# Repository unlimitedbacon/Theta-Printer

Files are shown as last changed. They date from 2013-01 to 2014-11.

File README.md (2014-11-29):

Theta Printer
=============

The Theta Printer is a platform for printing with as many different materials as possible. Whether it be different colors of plastic, wood, carbon fiber, chocolate, or anything else you can make an extruder for. Each extruder moves simultaneously and independently, allowing the printer to lay down 4 different materials onto the same object at the same time. [See it in action.](https://www.youtube.com/watch?v=p_tqMAzWGm0)

A magnificent rendering of the Theta Printer
[Full Size](http://i.imgur.com/XjrklZc.jpg)

With most 3D printers, adding more extruders makes the machine slower and reduces the build volume. The Theta Printer overcomes this by using polar coordinates. A polar printer works kind of like an old fashioned record player. Your objects are printed onto a platter which spins. The advantage is that you can have many print heads. Each extruder is on the end of an arm which swings in and out. The spinning platter is called the ϴ ("theta") axis and the swinging arm is called the R axis. Together these replace the normal X and Y coordinates you're used to. A polar printer has a couple of advantages over normal cartesian 3D printers.

1. Less moving mass means better acceleration
2. Finer resolution, especially near the center
3. Multiple toolheads without reducing build area

The spinning platform makes this machine ideal for integrating a 3D scanner. In addition, you can easily swap out an extruder for a mill or any other tool, making the Theta Printer the perfect all-in-one fabrication machine.

Specs
-----
+ 4 extruders for multiple colors and materials
+ 320 mm build platter
+ 80425 mm^2 print area (bigger than most repraps)
+ 0.084 degrees/step angular resolution (ϴ Axis)
+ 0.20 mm/step linear resolution (R Axis)
+ Now comes in two versions! The lasercut edition and the reprap edition (printed parts & threaded rods)

Links
-----
* [Development progress](http://forums.reprap.org/read.php?185,178379)
* [Videos](https://www.youtube.com/channel/UC-gtCzj4NQnUl9iEiGGx9JA/videos)
* [Firmware](https://github.com/unlimitedbacon/Marlin)

ϴ Axis
------
A wooden disk, under which resides a complicated set of motors gears rods and bearings
[Full Size](http://i.imgur.com/GR4uxWu.png)

Objects are printed onto a platter that spins back and forth. Its driven via a stepper motor and a large gear. Rollers support the platter around the perimeter and keep it level.

R Axis
------
Four robotic arms arranged in a diamond shape
[Full Size](http://i.imgur.com/bllIclA.png)

Four Extruders are each mounted on the end of an arm that swings in and out. The blue protractor things are gears for moving the arms.

Z Axis
------
A set of four sprockets with the associated pulleys, motors, and drive belt
[Full Size](http://i.imgur.com/wnbYKVQ.png)

The Z axis is nothing new. Threaded rods in each corner are synchronized by a timing belt and driven by two stepper motors.

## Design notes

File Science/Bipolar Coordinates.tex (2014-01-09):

\documentclass[12pt,letterpaper]{report}
\usepackage[utf8]{inputenc}
\usepackage{amsmath}
\usepackage{amsfonts}
\usepackage{amssymb}
\usepackage{graphicx}
\author{Tyler Anderson}
\title{Bipolar Coordinates}
\begin{document}
\section*{Coordinate Conversion}

First off, things are complicated because this machine doesn't truly use polar coordinates. Normal polar coordinates consist of an angle and a distance ($\theta$ and r). But in our case, the extruder arms move in an arc and not a straight line. This means that our coordinates have to be represented by two angles. $\theta_1$ is the angle of rotation of the platter. $\theta_2$ is the angle of the arm. Since this system has two poles, we'll call it bipolar coordinates. 

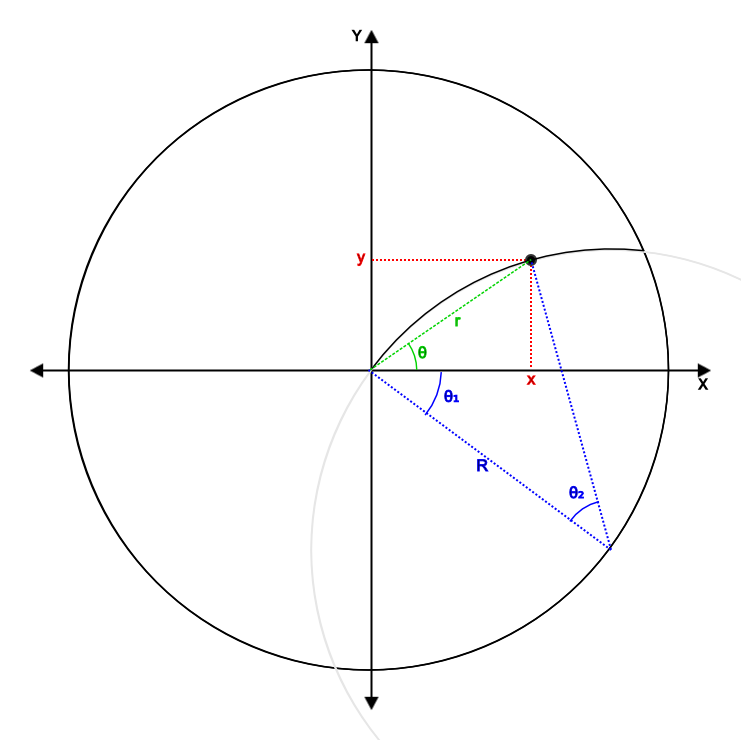
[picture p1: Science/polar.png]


In the above diagram, R is the length of the extruder arm which is 160mm on this machine. To simplify calculations all angles will be in radians.

The normal conversion from cartesian to polar is given by \ldots
\begin{equation}
	\theta = tan^{-1} \left( \dfrac{y}{x} \right)  
\end{equation}
\begin{equation}
	r = \sqrt{x^{2}+y^{2}}
\end{equation}

But for bipolar coordinates the conversion is \ldots
\begin{equation}
	\theta_2 = 2 sin^{-1} \left( \dfrac{\sqrt{x^2+y^2}}{2R} \right)
\end{equation}
\begin{equation}
	\theta_1 = \dfrac{\pi-\theta_2}{2} - tan^{-1} \left( \dfrac{y}{x} \right) 
\end{equation}

\section*{Parametric Equations}
We can now convert coordinates directly from cartesian to bipolar form, but more importantly, we need to know how to make the machine move in a straight line. Motion in 2D space is described using parametric equations. The equations for moving in a straight line in cartesian space are \ldots
\begin{equation}
	x = V_x t + x_0
\end{equation}
\begin{equation}
	y = V_y t + y_0
\end{equation}
\ldots where t is time, $V_x$ \& $V_y$ are the velocities in the $x$ and $y$ directions, and $x_0$ \& $y_0$ are the starting points.

By substituting these into the conversion for bipolar coordinates, we get the equations for linear motion in bipolar space.
\begin{equation}
	\theta_2 = 2 sin^{-1} \left(  \frac{\sqrt{(V_xt+x_0)^2 + (V_yt+y_0)^2}}{2R} \right)
\end{equation}
\begin{equation}
	\theta_1 = \frac{\pi-\theta_2}{2R} - tan^{-1} \left( \frac{V_y t + y_0}{V_x t + x_0} \right)
\end{equation}

\section*{Time}
The axes on the machine are controlled by stepper motors. Unlike most electric motors which run continuously when they are turned on, stepper motors move in small increments. In order to drive the motors, the controller needs to know exactly when to make each step. Since we know what the location of each axis will be after each step, we can solve for $t$ in the parametric equations to find out when to pulse the motors.

For $\theta_2$ the parametric equation is parabolic, so we must use the quadratic formula. The solution is broken down into components for simplicity.
\begin{equation}
	t_2 = \frac{-b\pm\sqrt{b^2-4ac}}{2a}
\end{equation}
\begin{equation}
	a = V_x^2+V_y^2
\end{equation}
\begin{equation}
	b = 2(V_x x_0 + V_y y_0)
\end{equation}
\begin{equation}
	c = x_o^2 + y_0^2 - 4R^2sin^2 \left( \frac{\theta_2}{2} \right)
\end{equation}

Remember that in the above equations, $\theta_2$ is the point after the next step will be made. It is easily determined by
\begin{equation}
	\theta_{2,n+1} = \theta_{2,n} \pm \Delta\theta_2
\end{equation}
where $\Delta\theta_2$ is the distance that axis moves with each step. $\Delta\theta_2$ is governed by the gear ratio and the number of steps per revolution of the motor.

The reason for the $\pm$ above is because we do not know in which direction the axis is moving (forward or backward) or if it will reverse direction before the step occurs. This means there are two possibilities. Combined with the two possible outcomes of the quadratic, this means that we can get up to 4 values for $t_2$. So which one do we choose? We use the lowest value that is still in the future ($> t$).

Now lets solve for $t$ in $theta_1$
\begin{equation}
	t_1 = \frac{x_0 * tan\left( \frac{\pi-\theta_2}{2} - \theta_1 \right) - y_0}{v_y - v_x * tan\left( \frac{\pi-\theta_2}{2} - \theta_1 \right)}
\end{equation}

But there is a problem. $\theta_1$ is dependent on $\theta_2$. In order to find $t$ we need to know $\theta_2$, but in order to get $\theta_2$ we need to know $t$. The solution we used is crude but effective. Instead of waiting until a certain time to make the step, the software periodically checks what the position of $\theta_1$ should be based on the current time. If the difference between the current and ideal positions is too great, it makes the step.

\section*{Derivatives}
It is also important for the software to know in which direction to move the motors, forward or reverse. When moving in a straight line in cartesian space, the direction is always the same. But in bipolar space, the direction can reverse in the middle of a move. In order to determine which way to go, we must find the signs of the derivatives of the parametric equations.

These are the derivatives. Here $x$ and $y$ are given by equations (5) and (6).
\begin{equation}
	\dfrac{d\theta_2}{dt} = \dfrac{2V_xx+2V_yy}{2R\sqrt{x^2+y^2}\sqrt{1-\dfrac{x^2+y^2}{4R^2}}}
\end{equation}
\begin{equation}
	\dfrac{d\theta_1}{dt} = -\left( \dfrac{1}{1-\dfrac{x^2+y^2}{4R^2}} \right) \left( \dfrac{(V_x^2+V_y^2)t+x_0V_x+y_0V_y}{2R\sqrt{x^2+y^2}} \right) - \left( \dfrac{1}{1+\left(\dfrac{y}{x}\right)^2} \right) \left( \dfrac{V_yx_0-V_xy_0}{x^2} \right) 
\end{equation}
\end{document}]{article}

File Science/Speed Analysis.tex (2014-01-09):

\documentclass[12pt,letterpaper]{report}
\usepackage[utf8]{inputenc}
\usepackage{amsmath}
\usepackage{amsfonts}
\usepackage{amssymb}
\usepackage{graphicx}
\usepackage{hyperref}
\author{Tyler Anderson}
\title{Theta Printer Speed Analysis}
\begin{document}

\maketitle

\section*{Speed Analysis}
The greatest limiting factor on the speeds of a 3D printer is the acceleration.

Older firmwares did not implement acceleration, so any changes in velocity would have to happen within the span of a single step. This limited the maximum speed of most printers to about 50 mm/s. While the motors and drive might be capable of much greater sustained speeds, the motor would not have enough torque to overcome the inertia of the moving parts, causing it to skip steps. Today's firmwares implement acceleration over multiple steps. By gradually ramping up the velocity, much higher maximum speeds can be achieved.

Today, the fastest reliable printer is probably the Ultimaker.

\subsection*{Motor Torque}
The RepRap forums recommend using stepper motors with a holding torque between 0.137 and 0.4 Newton-Meters \cite{rtorque}. Typical values for a NEMA 17 seem to be between 0.4 and 0.5 Nm \cite{htorque}. Our chosen motors are the NEMA 17s sold by Lulzbot with an advertised holding torque of 0.55 Nm.

Unfortunately, the torque exerted by a motor varies with speed. Also, torque while in motion is always significantly less than the holding torque. The datasheet for our chosen motors \cite{lulzmotor} provides a graph of the torque curve. At high speed the torque ranges from 0.25 to 0.20 Nm. We will accept 0.225 Nm as the average value.
\begin{equation}
	\tau = 0.225~\mathrm{Nm}
\end{equation}

% Probably uneccesary since torque at the platter can be found directly from the gear ratio
\subsection*{Motor Force}
In order to find the force exerted by the motor, we must first determine the radius of the motor gear. We use 18~tooth gears with a 2~mm pitch.
\begin{equation}
	r = \dfrac{18~\mathrm{teeth}*2.00~\dfrac{\mathrm{mm}}{\mathrm{tooth}}}{2\pi} = 5.73~\mathrm{mm} = 0.00573~\mathrm{m}
\end{equation}
\begin{equation}
	F = \dfrac{\tau}{r} = \dfrac{0.225~\mathrm{Nm}}{0.00573~\mathrm{m}} = 39.3~\mathrm{N}
\end{equation}

\subsection*{Mass Moment of Inertia}
Solidworks provides these figures based on the CAD model. $I_p$ will be the mass moment of inertia of the platter and associated moving parts.
% Needs to be redone since we changed to the aluminium platter
\begin{equation}
	I_p = ~\mathrm{kg*mm^2}
\end{equation}

It is slightly more difficult to get the figure for an extruder arm because the CAD model does not include the extruder itself. We must estimate the MMI of an extruder around the appropriate axis and add it to the figure given by Solidworks.

Approximating the extruder as a point mass:
\begin{equation}
	I_e = mr^2 = 
\end{equation}

Adding to the figure given for the arm by Solidworks, we get the total mass moment of inertia for the extruder arm.
\begin{equation}
	I_a = 0.00370601782~\mathrm{kg*m^2} +
\end{equation}

\subsection*{Final Torque}
The torque exerted on the platter and arms can be directly calculated from the motor torque and gear ratios.

For the platter:
\begin{equation}
	\tau_p = \tau \dfrac{N_2}{N_1} = 0.225~\mathrm{Nm} * \dfrac{385~\mathrm{teeth}}{18~\mathrm{teeth}} = 4.81~\mathrm{Nm}
\end{equation}

For the arm:
\begin{equation}
	\tau_a = \tau \dfrac{N_2}{N_1} = 0.225~\mathrm{Nm} * \dfrac{450~\mathrm{teeth}}{18~\mathrm{teeth}} = 5.63~\mathrm{Nm}
\end{equation}

\subsection*{Acceleration}
The angular acceleration can be found by the angular adaption of Newton's second law.
\begin{equation}
	\tau = I\alpha
\end{equation}

For the platter:
\begin{equation}
	\alpha_p = \dfrac{\tau_p}{I_p} = \dfrac{4.81~\mathrm{Nm}}{•} = ~\mathrm{\dfrac{rad}{s^2}}
\end{equation}

For the arm:
\begin{equation}
	\alpha_a = \dfrac{\tau_a}{I_a} = \dfrac{5.63~\mathrm{Nm}}{•} = ~\mathrm{\dfrac{rad}{s^2}}
\end{equation}

Since the extruder is fixed on the end of the arm, and the radius is constant, we can calculate the linear acceleration of the $\theta_2$ axis.
\begin{equation}
	a = \alpha r
\end{equation}
\begin{equation}
	a_a = ~\mathrm{\dfrac{rad}{s^2}} * 160~\mathrm{mm} = ~\mathrm{\dfrac{mm}{s^2}}
\end{equation}

For comparison, we can also calculate the linear acceleration of the $theta_1$ axis at a certain radius. The printer is designed to match the resolution of a RepRap at $r=122.55~\mathrm{mm}$.
\begin{equation}
	a_p = ~\mathrm{\dfrac{rad}{s^2}} * 122.55~\mathrm{mm} = ~\mathrm{\dfrac{mm}{s^2}}
\end{equation}
Closer to the center the acceleration will be less, but farther from the center it will be greater.

\subsection*{Equivalent Mass}
For comparison with other printers, we can also calculate the equivalent mass of each axis. These are the masses that a Cartesian printer would have to have to achieve the same acceleration.

\begin{equation}
	m = \dfrac{F}{a}
\end{equation}
X axis:
\begin{equation}
	m_x = \dfrac{39.3~\mathrm{N}}{~\mathrm{\dfrac{mm}{s^2}}} = ~\mathrm{g}
\end{equation}
Y axis:
\begin{equation}
	m_y = \dfrac{39.3~\mathrm{N}}{~\mathrm{\dfrac{mm}{s^2}}} = ~\mathrm{g}
\end{equation}

\section*{Comparison with Current RepRaps}
\subsection*{Mass of Moving Components}
\begin{tabular}{c|c|c}
& X Axis (g) & Y Axis (g) \\ 
\hline 
Modified Sells Mendel & 700 & 1300 \\ 
\hline 
Printxel & 400 & 800 \\ 
\end{tabular}

\subsection*{Acceleration}
\begin{tabular}{c|c}
Firmware & Acceleration ($mm/s^2$) \\
\hline
Marlin Defaults \cite{marlin} & 3000 \\
\hline
Safe Values for RepRap & 1500 \\
\hline
Ultimaker & 4600 \\
\hline
Accelerated Ultimaker \cite{ultimax} & 8000 \\
\hline
Cupcake w/o Acceleration & 38400 \\
\end{tabular}

\begin{thebibliography}{99}
\bibitem{rtorque} \url{http://reprap.org/wiki/Stepper_motor#Holding_Torque}
\bibitem{htorque} \url{http://reprap.org/wiki/Stepper_motor#NEMA_17_suppliers}
\bibitem{lulzmotor} \url{http://download.lulzbot.com/AO-100/hardware/electronics/spec_sheets/SY42STH47-1504A_stepperMotors.pdf}
\bibitem{marlin} \url{https://github.com/ErikZalm/Marlin/blob/Marlin_v1/Marlin/Configuration.h}
\bibitem{ultimax} \url{http://www.youtube.com/watch?v=i3DGRFMsU00}
\end{thebibliography}

\end{document}

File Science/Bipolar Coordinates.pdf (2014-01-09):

## Coordinate Conversion

First off, things are complicated because this machine doesn’t truly use polar coordinates. Normal polar coordinates consist of an angle and a distance (θ and r). But in our case, the extruder arms move in an arc and not a straight line. This means that our coordinates have to be represented by two angles. θ1 is the angle of rotation of the platter. θ2 is the angle of the arm. Since this system has two poles, we’ll call it bipolar coordinates.

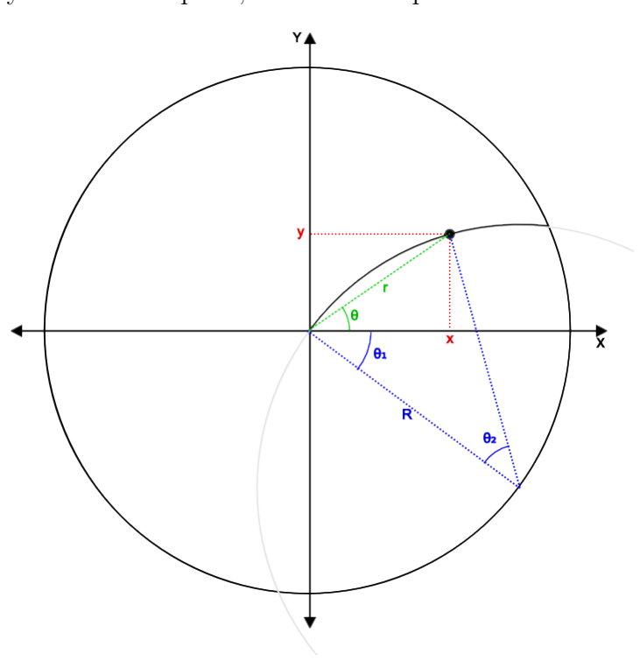
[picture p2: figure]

In the above diagram, R is the length of the extruder arm which is 160mm on this machine. To simplify calculations all angles will be in radians.
The normal conversion from cartesian to polar is given by . . .

θ = tan⁻¹

y
x
(1)

r =

p
x

2 + y

2
(2)

1

But for bipolar coordinates the conversion is . . .

θ2 = 2sin⁻¹

p
x

2 + y

2
2R

!
(3)

θ1 =

π − θ2
2

− tan⁻¹

y
x
(4)

## Parametric Equations

We can now convert coordinates directly from cartesian to bipolar form, but more importantly, we need to know how to make the machine move in a straight line. Motion in 2D space is described using parametric equations. The equations for moving in a straight line in cartesian space are . . .

x = Vxt + x0 | (5)
y = Vyt + y0 | (6)

. . . where t is time, Vx & Vy are the velocities in the x and y directions, and x0 & y0 are the starting points.
By substituting these into the conversion for bipolar coordinates, we get the equations for linear motion in bipolar space.

θ2 = 2sin⁻¹

p
(Vxt + x0)

2 + (Vyt + y0)

2
2R

!
(7)

θ1 =

π − θ2
2R

− tan⁻¹

Vyt + y0
Vxt + x0
(8)

## Time

The axes on the machine are controlled by stepper motors. Unlike most elec-tric motors which run continuously when they are turned on, stepper motors move in small increments. In order to drive the motors, the controller needs to know exactly when to make each step. Since we know what the location of each axis will be after each step, we can solve for t in the parametric equations to find out when to pulse the motors.

2

For θ2 the parametric equation is parabolic, so we must use the quadratic formula. The solution is broken down into components for simplicity.

t2 =

−b ±

√
b

2 − 4ac
2a

(9)

a = V

2
x + V

2
y

(10)

b = 2(Vxx0 + Vyy0) | (11)

c = x

2
o + y

2
0 − 4R

2

sin²

θ2
2
(12)

Remember that in the above equations, θ2 is the point after the next step will be made. It is easily determined by

θ2,n+1 = θ2,n ± ∆θ2 | (13)

where ∆θ2 is the distance that axis moves with each step. ∆θ2 is governed by the gear ratio and the number of steps per revolution of the motor.
The reason for the ± above is because we do not know in which direction the axis is moving (forward or backward) or if it will reverse direction before the step occurs. This means there are two possibilities. Combined with the two possible outcomes of the quadratic, this means that we can get up to 4 values for t2. So which one do we choose? We use the lowest value that is still in the future (> t).
Now lets solve for t in theta1

t1 =

x0 ∗ tan

π−θ2
2 − θ1
− y0
vy − vx ∗ tan

π−θ2
2 | − θ1
| (14)

But there is a problem. θ1 is dependent on θ2. In order to find t we need to know θ2, but in order to get θ2 we need to know t. The solution we used is crude but effective. Instead of waiting until a certain time to make the step, the software periodically checks what the position of θ1 should be based on the current time. If the difference between the current and ideal positions is too great, it makes the step.

3

## Derivatives

It is also important for the software to know in which direction to move the motors, forward or reverse. When moving in a straight line in cartesian space, the direction is always the same. But in bipolar space, the direction can reverse in the middle of a move. In order to determine which way to go, we must find the signs of the derivatives of the parametric equations. These are the derivatives. Here x and y are given by equations (5) and (6).
dθ2
dt =

2Vxx + 2Vyy

2R

p
x

2 + y

2

r
1 −

x

2 + y

2
4R²

(15)

dθ1
dt = −

1

1 −

x

2 + y

2
4R²

(V

2
x + V

2
y

)t + x0Vx + y0Vy

2R

p
x

2 + y

2

!
−

1
1 + y
x

2

Vyx0 − Vxy0
x

2

(16)

4

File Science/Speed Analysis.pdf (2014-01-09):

# Theta Printer Speed Analysis

### Tyler Anderson

### November 29, 2013

## Speed Analysis

The greatest limiting factor on the speeds of a 3D printer is the acceleration. Older firmwares did not implement acceleration, so any changes in velocity would have to happen within the span of a single step. This limited the maximum speed of most printers to about 50 mm/s. While the motors and drive might be capable of much greater sustained speeds, the motor would not have enough torque to overcome the inertia of the moving parts, caus-ing it to skip steps. Today’s firmwares implement acceleration over multiple steps. By gradually ramping up the velocity, much higher maximum speeds can be achieved.
Today, the fastest reliable printer is probably the Ultimaker.

### Motor Torque

The RepRap forums recommend using stepper motors with a holding torque between 0.137 and 0.4 Newton-Meters [1]. Typical values for a NEMA 17 seem to be between 0.4 and 0.5 Nm [2]. Our chosen motors are the NEMA 17s sold by Lulzbot with an advertised holding torque of 0.55 Nm. Unfortunately, the torque exerted by a motor varies with speed. Also, torque while in motion is always significantly less than the holding torque. The datasheet for our chosen motors [3] provides a graph of the torque curve. At high speed the torque ranges from 0.25 to 0.20 Nm. We will accept 0.225 Nm as the average value.
τ = 0.225 Nm | (1)

### Motor Force

In order to find the force exerted by the motor, we must first determine the radius of the motor gear. We use 18 tooth gears with a 2 mm pitch.

r =

18 teeth ∗ 2.00

mm
tooth
2π
= 5.73 mm = 0.00573 m | (2)

F =

τ
r

=

0.225 Nm
0.00573 m
= 39.3 N | (3)

1

### Mass Moment of Inertia

Solidworks provides these figures based on the CAD model. Ip will be the mass moment of inertia of the platter and associated moving parts.

Ip = kg ∗ mm²
(4)

It is slightly more difficult to get the figure for an extruder arm because the CAD model does not include the extruder itself. We must estimate the MMI of an extruder around the appropriate axis and add it to the figure given by Solidworks.
Approximating the extruder as a point mass:
Ie = mr² = | (5)

Adding to the figure given for the arm by Solidworks, we get the total mass moment of inertia for the extruder arm.

Ia = 0.00370601782 kg ∗ m

2+ | (6)

### Final Torque

The torque exerted on the platter and arms can be directly calculated from the motor torque and gear ratios.
For the platter:

τp = τ

N2
N1

= 0.225 Nm ∗

385 teeth
18 teeth = 4.81 Nm | (7)

For the arm:

τa = τ

N2
N1

= 0.225 Nm ∗

450 teeth
18 teeth = 5.63 Nm | (8)

### Acceleration

The angular acceleration can be found by the angular adaption of Newton’s second law.
τ = Iα | (9)

For the platter:

αp =

τp
Ip

=

4.81 Nm
ffl

=

rad
s

2

(10)

2

For the arm:
αa =

τa
Ia

=

5.63 Nm
ffl

=

rad
s

2

(11)

Since the extruder is fixed on the end of the arm, and the radius is constant, we can calculate the linear acceleration of the θ2 axis.

a = αr | (12)

aa =

rad
s

2

∗ 160 mm =

mm
s

2

(13)

For comparison, we can also calculate the linear acceleration of the theta1 axis at a certain radius. The printer is designed to match the resolution of a RepRap at r = 122.55 mm.

ap =

rad
s

2

∗ 122.55 mm =

mm
s

2

(14)

Closer to the center the acceleration will be less, but farther from the center it will be greater.

### Equivalent Mass

For comparison with other printers, we can also calculate the equivalent mass of each axis. These are the masses that a Cartesian printer would have to have to achieve the same acceleration.

m =

F
a

(15)

X axis:
mx =

39.3 N
mm
s

2

= g | (16)

Y axis:
my =

39.3 N
mm
s

2

= g | (17)

3

## Comparison with Current RepRaps

### Mass of Moving Components

| X Axis (g) | Y Axis (g)
Modified Sells Mendel | 700 | 1300
Printxel | 400 | 800

### Acceleration

Firmware | Acceleration (mm/s²
)
Marlin Defaults [4] | | 3000
Safe Values for RepRap | | 1500
Ultimaker | | 4600
Accelerated Ultimaker [5] | | 8000
Cupcake w/o Acceleration | | 38400

4

# Bibliography

[1] http://reprap.org/wiki/Stepper_motor#Holding_Torque
[2] http://reprap.org/wiki/Stepper_motor#NEMA_17_suppliers
[3] http://download.lulzbot.com/AO-100/hardware/electronics/spec_sheets/SY42STH47-1504A_stepperMotors.pdf (http://download.lulzbot.com/AO-100/hardware/electronics/spec_sheets/SY42STH47-1504A_stepperMotors.pdf)
[4] https://github.com/ErikZalm/Marlin/blob/Marlin_v1/Marlin/Configuration.h (https://github.com/ErikZalm/Marlin/blob/Marlin_v1/Marlin/Configuration.h)
[5] http://www.youtube.com/watch?v=i3DGRFMsU00

5

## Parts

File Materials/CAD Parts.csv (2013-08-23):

ITEM NO. | PART NUMBER | DESCRIPTION | QTY.
1 | Head Holder |  | 8
2 | Arm Rod |  | 8
3 | M8.Nut |  | 149
4 | Arm Center |  | 4
5 | Arm Axis Rod |  | 4
6 | R Gear |  | 4
7 | M3x16.Bolt.91290A120 |  | 172
8 | Extruder Mount Plate |  | 4
9 | M4x30.Bolt.91280A148 |  | 8
10 | M4.Nut.90591A141 |  | 8
11 | Level 1 Corner |  | 8
12 | 608RS Bearing |  | 36
13 | 608 Bearing Cap |  | 1
14 | M3.Nut.90591A121 |  | 172
15 | R Motor Mount |  | 4
16 | Base |  | 7
17 | Cuerpo |  | 7
18 | Tapa |  | 7
19 | B18.6.7M - M3 x 0.5 x 5 Type I Cross Recessed PHMS --5N |  | 28
20 | Eje |  | 7
21 | AFBMA 12.1.4.1 - 0050-11 - 10 SI NC 10_68 |  | 14
22 | M3x10.Bolt.91290A115 |  | 28
23 | Motor.Sprocket |  | 7
24 | Theta Center |  | 1
25 | M3x30.Bolt.91290A130 |  | 4
26 | Level Z Corner |  | 4
27 | Linear Bearing Body |  | 8
28 | Linear Bearing inside |  | 8
29 | Platter Rod |  | 4
30 | Theta Motor Mount |  | 1
31 | Platter Top |  | 1
32 | Platter Bottom |  | 1
33 | M3x16.Countersunk.Bolt.91294A134 |  | 4
34 | Platter Axle |  | 1
35 | M8.Washer.91455A130 |  | 8
36 | Theta Gear |  | 1
37 | Platter Roller Mount High |  | 1
38 | M8x20.Bolt.91310A533 |  | 3
39 | Platter Roller Mount Low |  | 2
40 | Level 4 Corner |  | 4
41 | Z Smooth Rod |  | 8
42 | Z Rod |  | 4
43 | Z.Rod.Sprocket.a_6z51-036df0610 |  | 4
44 | Smooth Rod Clamp |  | 16
45 | Belt1-1 |  | 1
46 | Level 1 Side |  | 1
47 | Level 2 Side |  | 1
48 | Level 4 Side |  | 1
49 | M8x30.Bolt.91310A536 |  | 4
50 | Side 1 |  | 2
51 | Side 2 |  | 2
52 | 91166A210 |  | 8

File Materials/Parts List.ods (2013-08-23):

Acquired? | Printed Parts | Description | Qty
✓ | Head Holder |  | 8
✓ | Level 1 Corner |  | 8
✓ | Motor Sprocket |  | 7
✓ | Arm Center |  | 4
✓ | Level 4 Corner |  | 4
✓ | Level Z Corner |  | 4
✓ | R Motor Mount |  | 4
✓ | Z Rod Sprocket |  | 4
✓ | Platter Roller Middle |  | 3
✓ | Theta Center |  | 1
✓ | Theta Motor Mount |  | 1
 | Laser Cut Parts | Description | Qty | Cost
3 | R Gear | 5mm Acrylic | 4
✓ | Theta Gear | 5mm Acrylic | 1
✓ | Extruder Mount Plate | 5mm Plywood | 4
✓ | Platter Top | 5mm Plywood | 1
✓ | Platter Bottom | 5mm Plywood | 1
✓ | Level 1 Side | 5mm Plywood | 1
✓ | Level 2 Side | 5mm Plywood | 1
✓ | Level 4 Side | 5mm Plywood | 1
✓ | Side 1 | 5mm Plywood | 2
✓ | Side 2 | 5mm Plywood | 2
✓ | 608 Bearing Cap | 5mm Plywood | 1
✓ | Platter Roller Side High |  | 4
✓ | Platter Roller Side Low |  | 2
 | Total |  |  | $60
 | Threaded Rods | Description | Qty | Length (mm) | Total Length | Purchase Qty | Price/Meter | Subtotal
✓ | Arm Rod | M8 1.25 Pitch | 8 | 220 | 1760 | 2000
✓ | Arm Axis Rod | M8 1.25 Pitch | 4 | 110 | 440 | 1000
✓ | Platter Rod | M8 1.25 Pitch | 4 | 400 | 1600 | 2000
✓ | Platter Axle | M8 1.25 Pitch | 1 | 55 | 55 | 1000
✓ | Z Rod | M8 1.25 Pitch | 4 | 430 | 1720 | 2000
✓ | Total |  |  |  | 5575 | 8000 | 4.29 | $34.32 | McMaster | 99055A125 | http://www.mcmaster.com/#catalog/119/3147/=liic32
 | Smooth Rod
✓ | Z Smooth Rod | M8 | 8 | 350 | 2800 | 3200 |  | $49.56 | AliExpress | 707204369 | http://www.aliexpress.com/item/CNC-2pcs-Linear-shaft-400mm-long-diameter-8mm-L-400mm-harden-linear-rod-round-shaft-chrome/707204369.html
 |  |  |  |  |  | 12ft |  | $27.28 | McMaster | 89095K15 | http://www.mcmaster.com/#89095K15
 | Vitamins | Description | Qty | Purchase Qty | Price Each | Subtotal | Supplier | Part # | Link
✓ | 608ZZ Bearing |  | 28 | 50 |  | 22.5 | AliExpress | 609983490 | http://www.aliexpress.com/item/50pcs-lot-608ZZ-608-2RS-8-22-7-Deep-groove-ball-bearing-skate-wheel-bearing/609983490.html
✓ | LM8UU Linear Bearing |  | 8 | 20 |  | 13.8 | AliExpress | 488396282 | http://www.aliexpress.com/item/LM8UU-8mm-Linear-Ball-Bearing-Bush-Bushing-New/488396282.html
✓ | M3.Nut.90591A121 |  | 172 | 200 |  | 2.78 | McMaster | 90591A121 | http://www.mcmaster.com/#catalog/119/3167/=l4j9dm
✓ | M3x10.Bolt.91290A115 |  | 28 | 100 |  | 5.02 | McMaster | 91290A115 | http://www.mcmaster.com/#catalog/119/3093/=l4j9n6
✓ | M3x16.Bolt.91290A120 |  | 176 | 200 |  | 12.1 | McMaster | 91290A120 | http://www.mcmaster.com/#catalog/119/3093/=l4j9rl
✓ | M3x16.Countersunk.Bolt.91294A134 |  | 4 | 100 |  | 11.67 | McMaster | 91294A134 | http://www.mcmaster.com/#catalog/119/3102/=l4ja5r
✓ | M3x30.Bolt.91290A130 |  | 4 | 0 |  | 0 | McMaster | 91290A130 | http://www.mcmaster.com/#catalog/119/3093/=l4jb78
✓ | M4.Nut.90591A141 |  | 8 | 100 |  | 1.39 | McMaster | 90591A141 | http://www.mcmaster.com/#catalog/119/3167/=l4jbpz
✓ | M4x30.Bolt.91280A148 |  | 8 | 100 |  | 7.96 | McMaster | 91280A148 | http://www.mcmaster.com/#catalog/119/3129/=l4jcc0
✓ | M8.Nut | 1.25mm Pitch | 149 | 200 |  | 9.02 | McMaster | 90592A022 | http://www.mcmaster.com/#hex-nuts/=l4je22
✓ | M8.Washer.91455A130 |  | 8 | 100 |  | 6.09 | McMaster | 91455A130 | http://www.mcmaster.com/#catalog/119/3202/=l4jej3
✓ | M8x20.Bolt.91310A533 |  | 3 | 0 |  | 0 | McMaster | 91310A533 | http://www.mcmaster.com/#catalog/119/3128/=l4jf1j
✓ | M8x30.Bolt.91310A536 |  | 4 | 25 |  | 7.91 | McMaster | 91310A536 | http://www.mcmaster.com/#standard-cap-screws/=ld4026
 | Motor.Sprocket | 18 Grooves | 7 | 0 | 5.81 | 0 | SDP/SI | A 6T16M018DF6005 | https://sdp-si.com/eStore/PartDetail.asp?Opener=Group&PartID=42977&GroupID=347
✓ | Z Belt | GT2 1210.00 mm | 1 | 1 | 9.32 | 9.32 | SDP/SI | A 6R51M605060 | https://sdp-si.com/eStore/PartDetail.asp?Opener=Order&PartID=75945&GroupID=342&Qty=0
✓ | Z Belt | GT2 1228.00 mm | 1 | 1 | 9.32 | 9.32 | SDP/SI | A 6R51M614060 | https://sdp-si.com/eStore/PartDetail.asp?Opener=Order&PartID=75946&GroupID=342&Qty=0
 | Z.Rod.Sprocket | 36 Grooves | 4 | 0 | 6.18 | 0 | SDP/SI | A 6Z51-036DF0610 | https://sdp-si.com/eStore/PartDetail.asp?Opener=Group&PartID=55833&GroupID=218
 | Total |  |  |  |  | $118.88
 | Electronics | Description | Qty | Cost
✓ | ATX Power Supply |  | 1 | $100
 | Decapede Electronics |  | 1 | 250
 | Stepper Drivers | Polulu compatible | 10 | 99.5
6 | NEMA 17 Motors |  | 7 | 97.65
 |  |  |  | $547
 | Extruder Components |  | Qty | Price Each | Subtotal | Link
 | Printed Parts
✓ | Greg's Wade Reloaded Extruder |  | 4 |  |  | http://www.thingiverse.com/thing:18379
 | Hot End
✓ | Lulzbot Budaschnozzle |  | 4 | 95 | 380 | http://www.lulzbot.com/?q=products/budaschnozzle-20-w-035mm-nozzle
 | Extruder Motor
✓ | NEMA 17 |  | 4 | 13.95 | 55.8 | http://www.lulzbot.com/?q=products/nema-17-stepper-motors
 | Extruder Hardware
✓ | M8 Hobbed Bolt |  | 4 | 7 | 28 | http://www.lulzbot.com/?q=products/hobbed-bolt-stainless-steel
✓ | M8 Washer |  | 16
✓ | M3x8 Bolt |  | 12
✓ | M3x30 Bolt |  | 4
✓ | M3 Nut |  | 4
✓ | M3 Washer |  | 16
✓ | M4x55 Bolt |  | 8
✓ | M4x20 Bolt | Duplicate? | 8
✓ | M4 Nut | Duplicate? | 16
✓ | 608ZZ Bearing |  | 12
✓ | M8x20 Rod |  | 4
✓ | Spring | .297OD, .049WD, .669FL? | 8
 |  |  |  |  | 463.8
 | Grand Total | $1,274

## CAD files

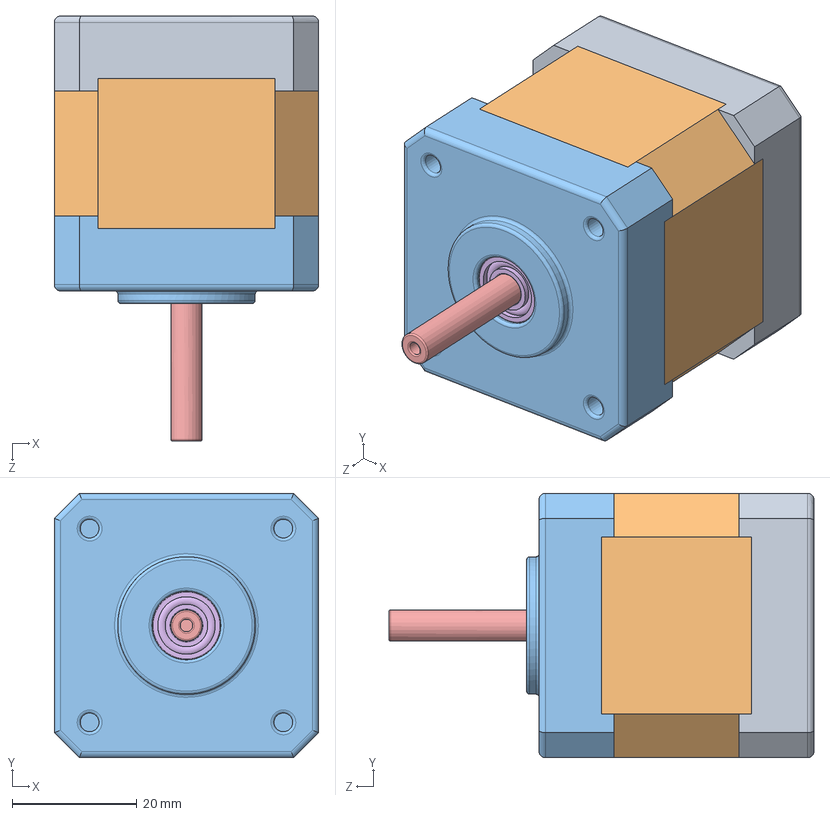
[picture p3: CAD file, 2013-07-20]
Vitamins/NEMA 17/NEMA 17.SLDASM
42.3 x 42.3 x 68.0 mm
Base
Cuerpo
Tapa
pan cross head_am
Eje
instrument ball bearing_68_am

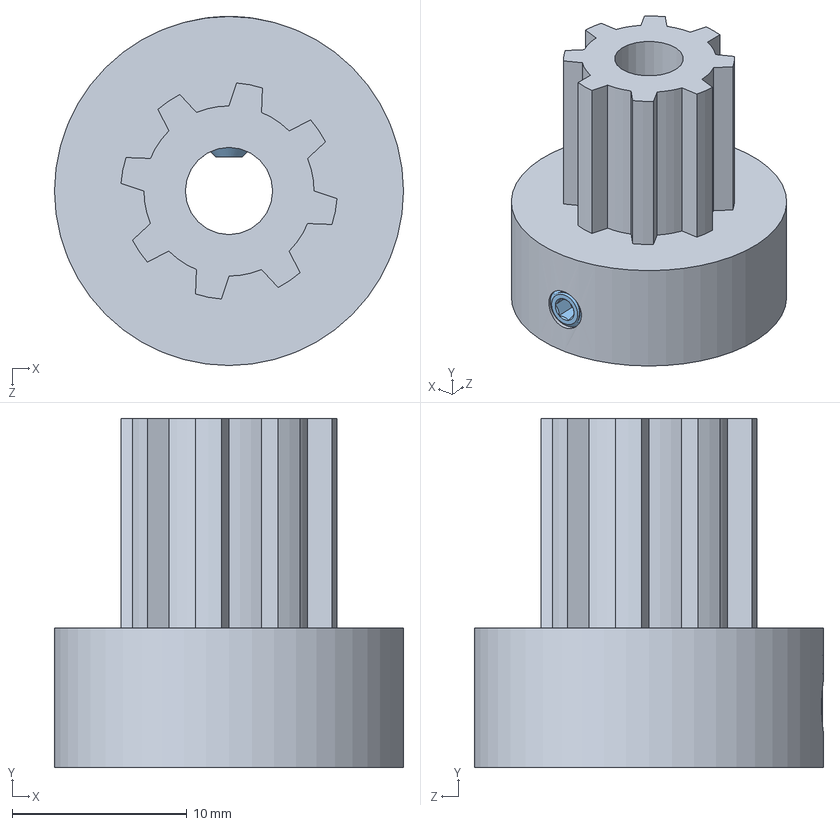
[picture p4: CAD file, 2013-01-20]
Vitamins/FULLER_LOCK_PULLEY/FULLER LOCK PULLEY.SLDASM
20.0 x 20.0 x 20.0 mm
FULLER LOCK PULLEY
3mm Nylon Nut
3mm X 8 SET SCREW ( Mcmaster 92015A105)

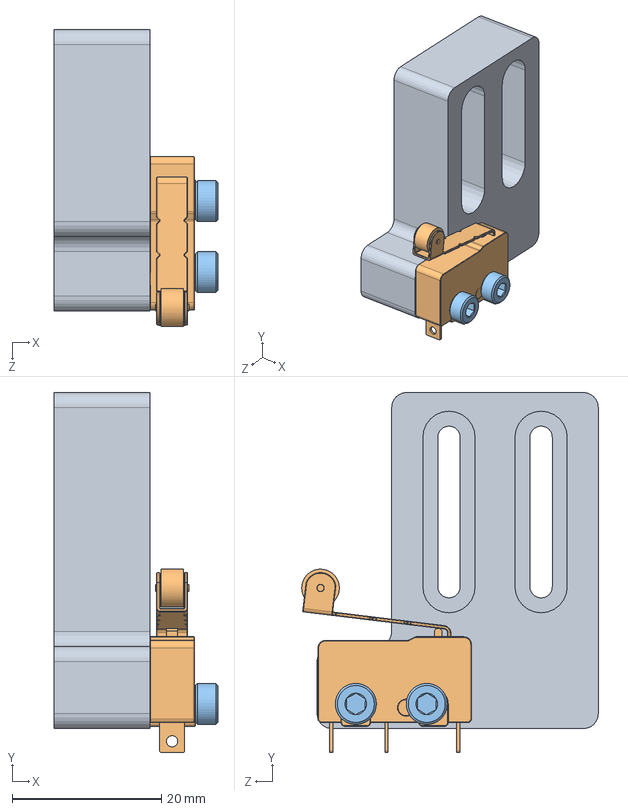
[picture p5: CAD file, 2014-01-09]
Endstop Mount Assembly.SLDASM
21.9 x 48.2 x 39.7 mm
Endstop Mount
SM5.Microswitch
M3x16.Bolt.91290A120 x 2

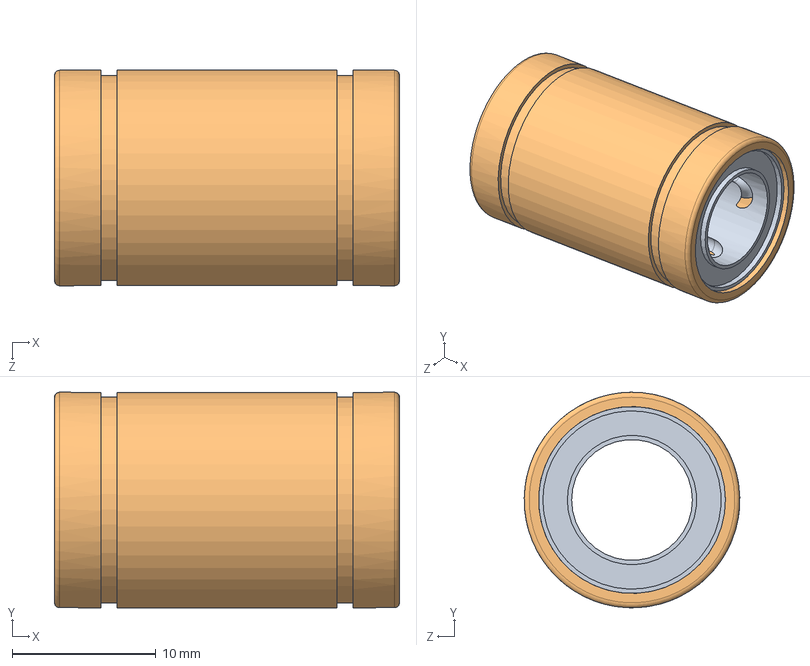
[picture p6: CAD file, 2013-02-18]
Vitamins/LM8UU/Linear Bearing animation.SLDASM
24.0 x 15.0 x 15.0 mm
Linear Bearing Body
Linear Bearing inside

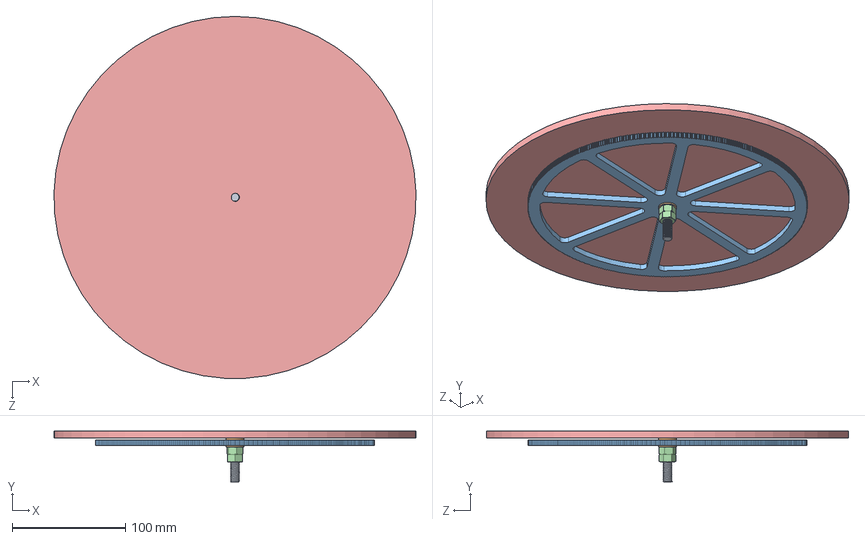
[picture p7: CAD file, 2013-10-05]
Platter Assembly.SLDASM
319.9 x 45.0 x 320.0 mm
Platter Axle
M8.Washer.91455A130 x 2
Theta Gear
M8.Nut x 2
Platter

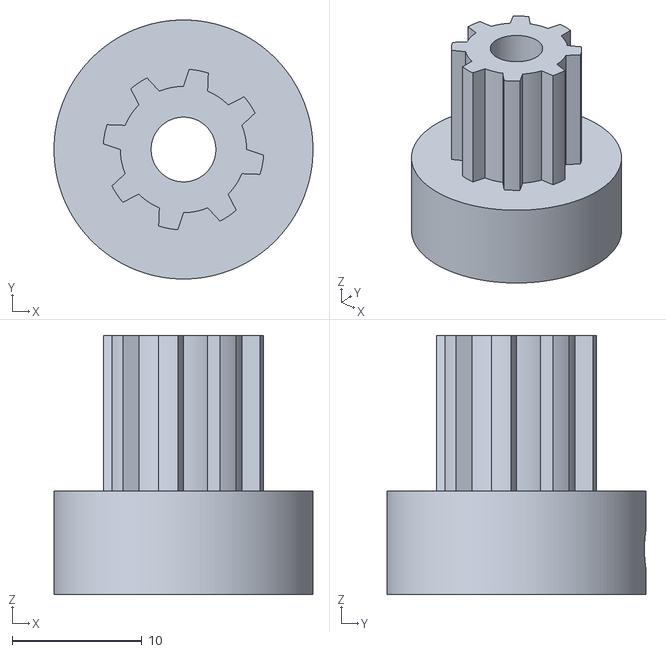
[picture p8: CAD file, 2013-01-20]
Vitamins/FULLER_LOCK_PULLEY/FULLER_LOCK_PULLEY_OVERSIZED.STL
20.0 x 20.0 x 20.0

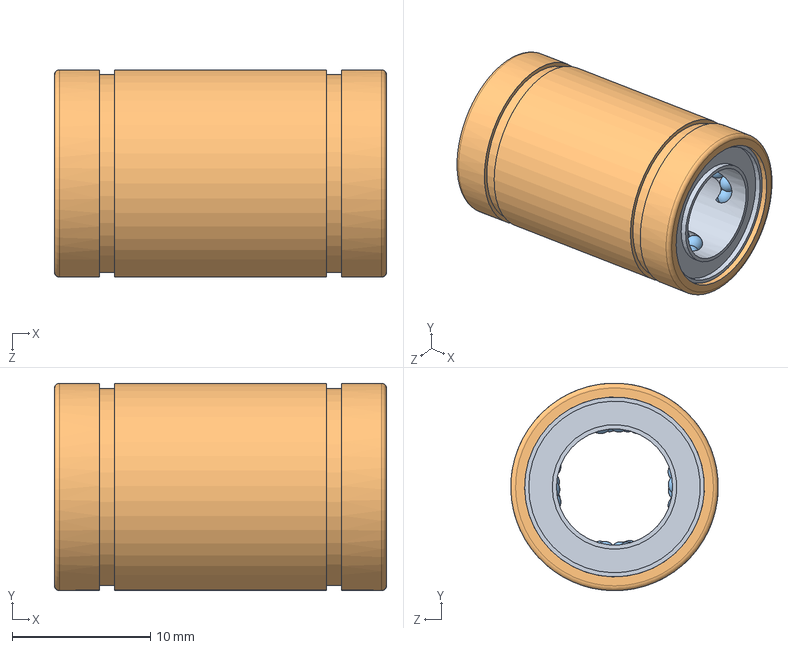
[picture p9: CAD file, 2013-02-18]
Vitamins/LM8UU/LU8MM.SLDASM
24.0 x 15.0 x 15.0 mm
Linear Bearing Body
Linear Bearing inside
Municion x 102

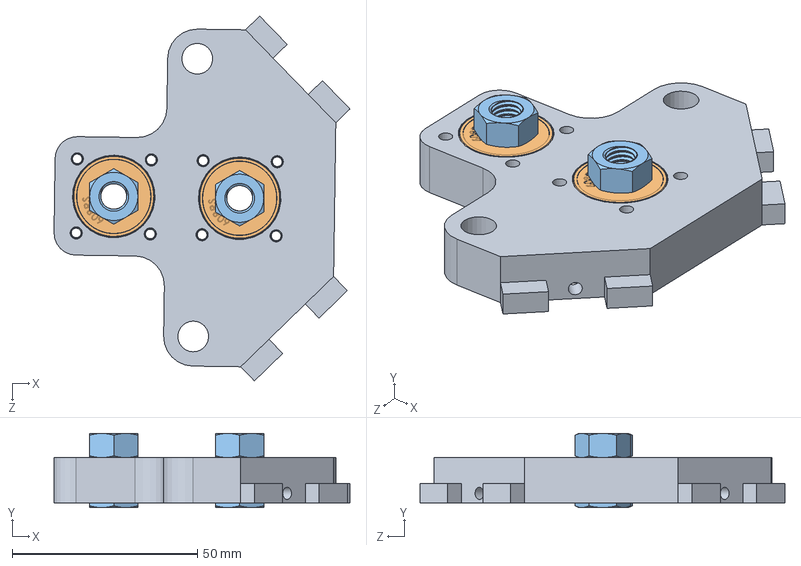
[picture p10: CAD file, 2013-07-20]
Level 1 Corner Assembly.SLDASM
79.9 x 20.0 x 98.5 mm
Level 1 Corner
608RS Bearing x 2
M8.Nut x 4
M3.Nut.90591A121 x 8

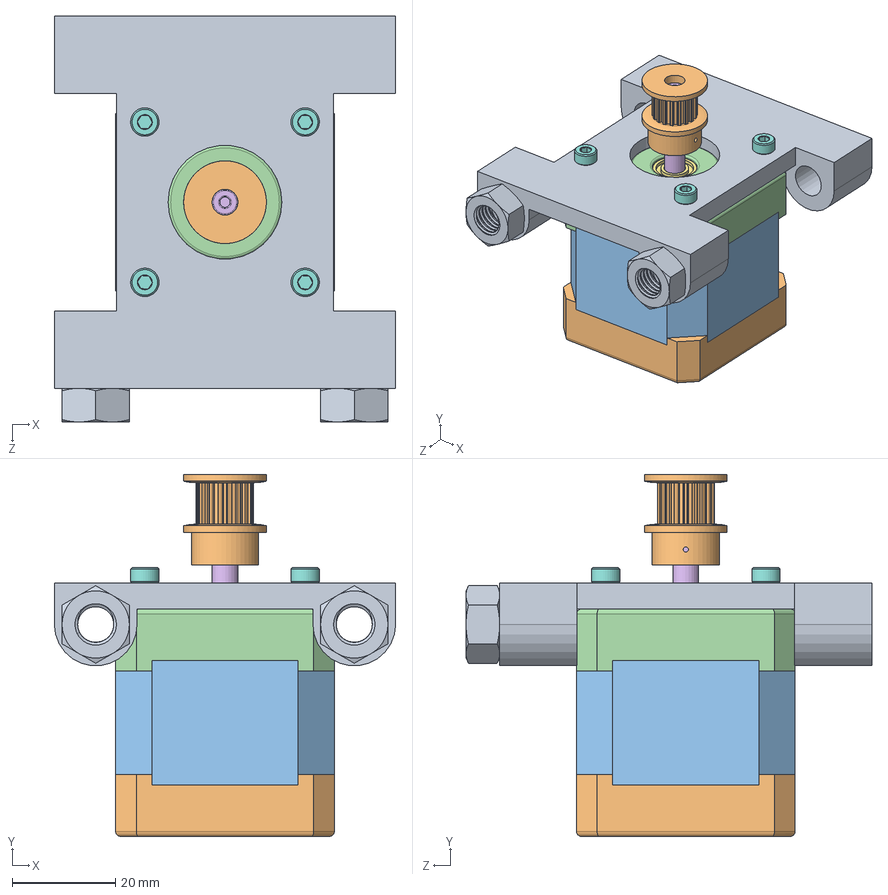
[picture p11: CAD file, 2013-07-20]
Theta Motor Assembly.SLDASM
66.0 x 70.0 x 78.5 mm
Theta Motor Mount
Base
Cuerpo
Tapa
pan cross head_am
Eje
instrument ball bearing_68_am
M3x10.Bolt.91290A115 x 4
M8.Nut x 2
Motor.Sprocket

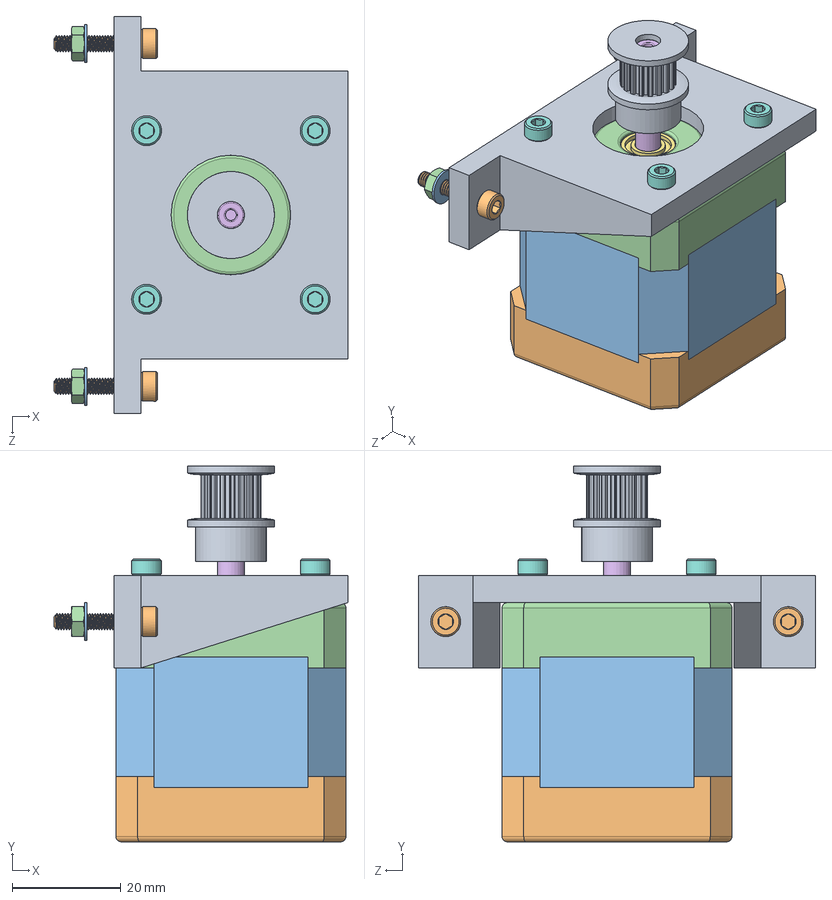
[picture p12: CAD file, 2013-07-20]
R Motor Assembly.SLDASM
54.0 x 69.1 x 73.0 mm
R Motor Mount
Base
Cuerpo
Tapa
pan cross head_am
Eje
instrument ball bearing_68_am
M3x10.Bolt.91290A115 x 4
Motor.Sprocket
M3x16.Bolt.91290A120 x 2
M3.Washer.91166A210 x 2
M3.Nut.90591A121 x 2

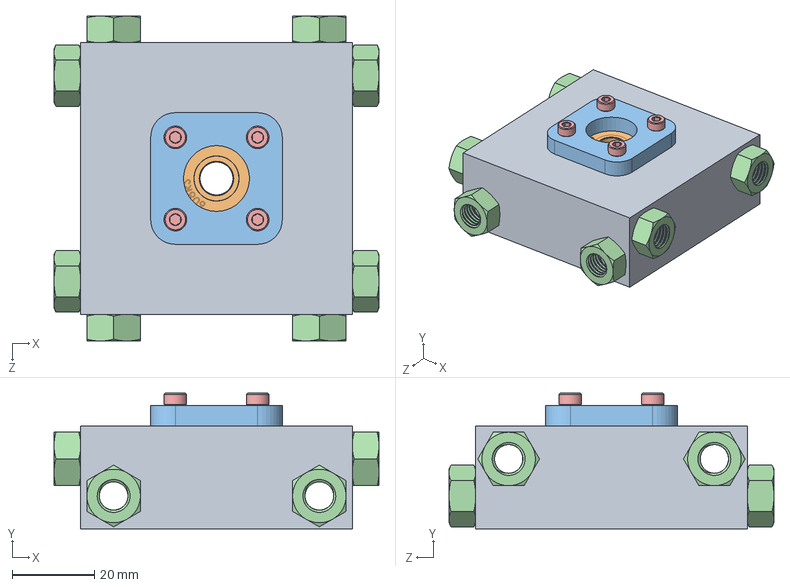
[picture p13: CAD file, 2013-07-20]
Theta Center Assembly.SLDASM
79.0 x 33.0 x 79.0 mm
Theta Center
608RS Bearing
608 Bearing Cap
M8.Nut x 8
M3x16.Bolt.91290A120 x 4
M3.Nut.90591A121 x 4

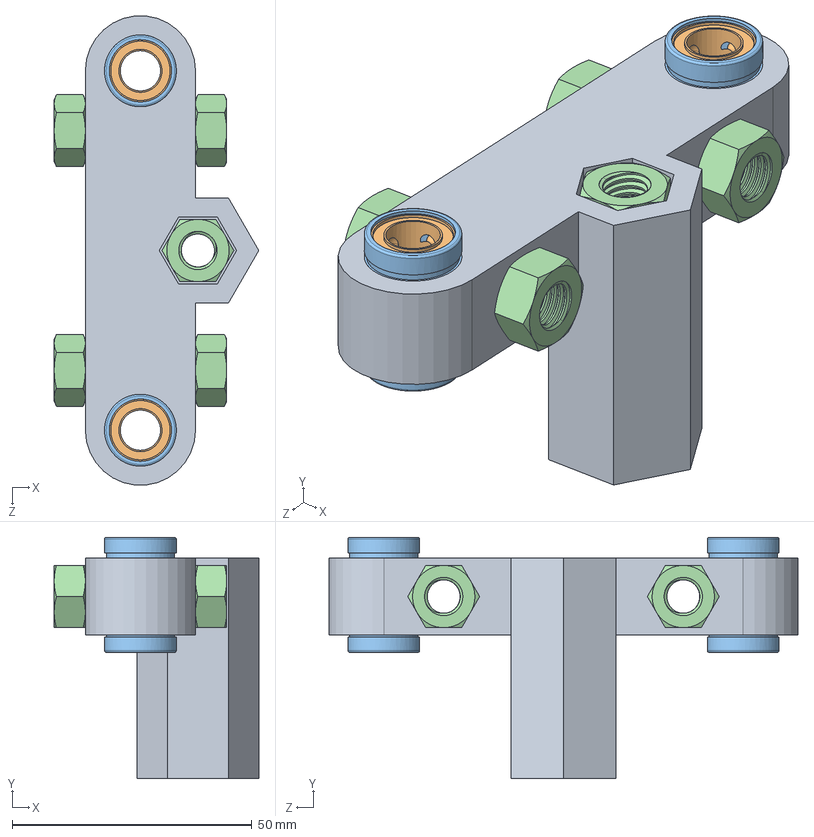
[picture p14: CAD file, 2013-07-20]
Level Z Corner Assembly.SLDASM
42.7 x 50.3 x 97.9 mm
Level Z Corner
Linear Bearing Body x 2
Linear Bearing inside x 2
M8.Nut x 5

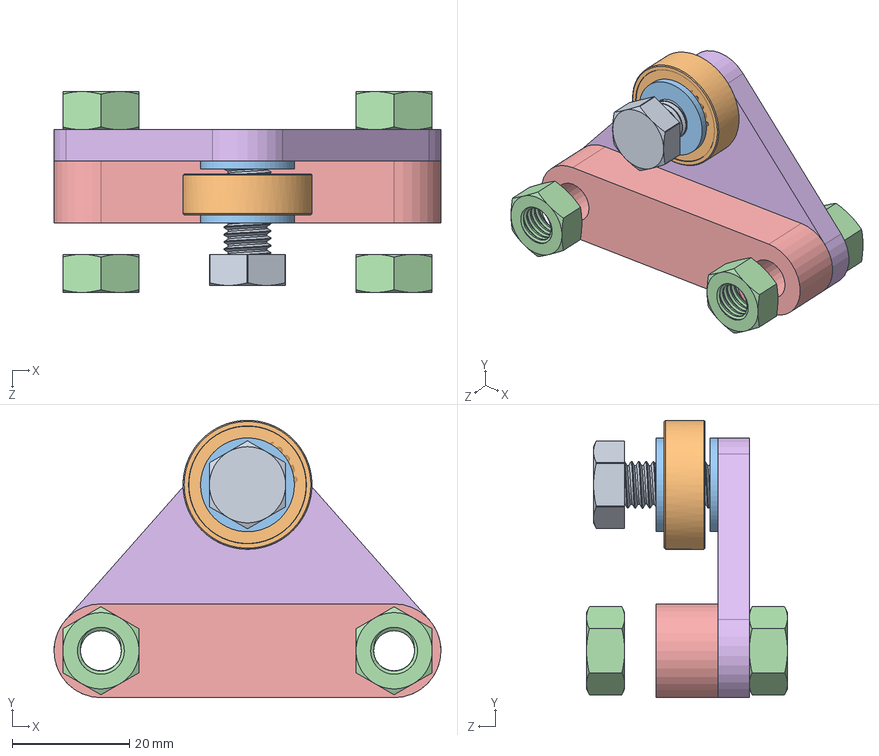
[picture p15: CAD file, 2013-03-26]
Platter Roller Assembly.SLDASM
66.0 x 47.3 x 34.3 mm
M8x20.Bolt.91310A533
608RS Bearing
M8.Washer.91455A130 x 2
M8.Nut x 4
Platter Roller Middle
Platter Roller Side

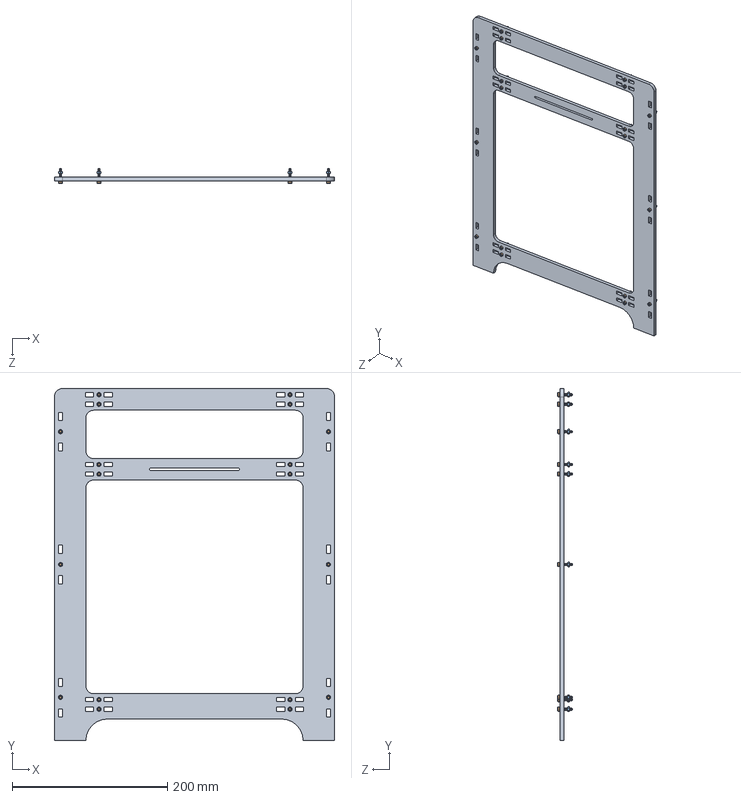
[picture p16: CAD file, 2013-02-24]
Side 2 Assembly.SLDASM
361.3 x 453.7 x 19.0 mm
Side 2
M3x16.Bolt.91290A120 x 18
M3.Nut.90591A121 x 18

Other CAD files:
Vitamins/LM8UU/LM8UU.SLDASM
Side 1 Assembly.SLDASM
Smooth Rod Clamp Assembly.SLDASM
Platter Roller Assembly High.SLDASM
608 Bearing Cap.SLDPRT
Arm Center.SLDPRT
Belt1-1.sldprt
Bottom Sketch.SLDPRT
DXFs/608 Bearing Cap.DXF
DXFs/Extruder Mount Plate.DXF
DXFs/Level 1 Side.DXF
DXFs/Level 2 Side.DXF
DXFs/Level 4 Side.DXF
DXFs/Platter Bottom.DXF
DXFs/Platter Roller Side.High.DXF
DXFs/Platter Roller Side.Low.DXF
DXFs/Platter Top.DXF
DXFs/R Gear.DXF
DXFs/Side 1.DXF
DXFs/Side 2.DXF
DXFs/Theta Gear.DXF
Endstop Mount.SLDPRT
Endstop Mount.STP
Extruder Fan Mount.SLDPRT
Extruder Fan Mount.stp
Extruder Mount Plate.SLDPRT
Head Holder.SLDPRT
Level 1 Corner.SLDPRT
Level 1 Side.SLDPRT
Level 2 Side.SLDPRT
Level 4 Corner.SLDPRT
Level 4 Side.SLDPRT
Level Z Corner.SLDPRT
Materials/CAD Parts.SLDDRW
Platter Roller Assembly Low.SLDASM
Platter Roller Middle.SLDPRT
Platter Roller Mount High.SLDPRT
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

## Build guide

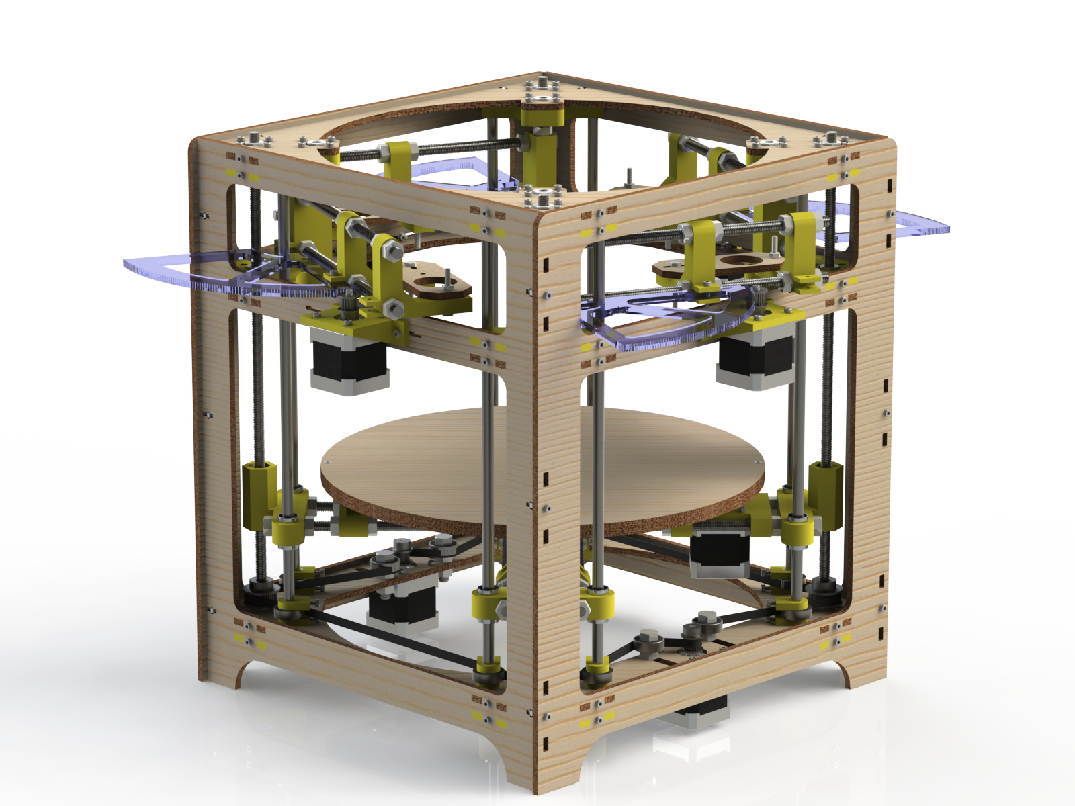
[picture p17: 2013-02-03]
Renders/theta_printer_12.png

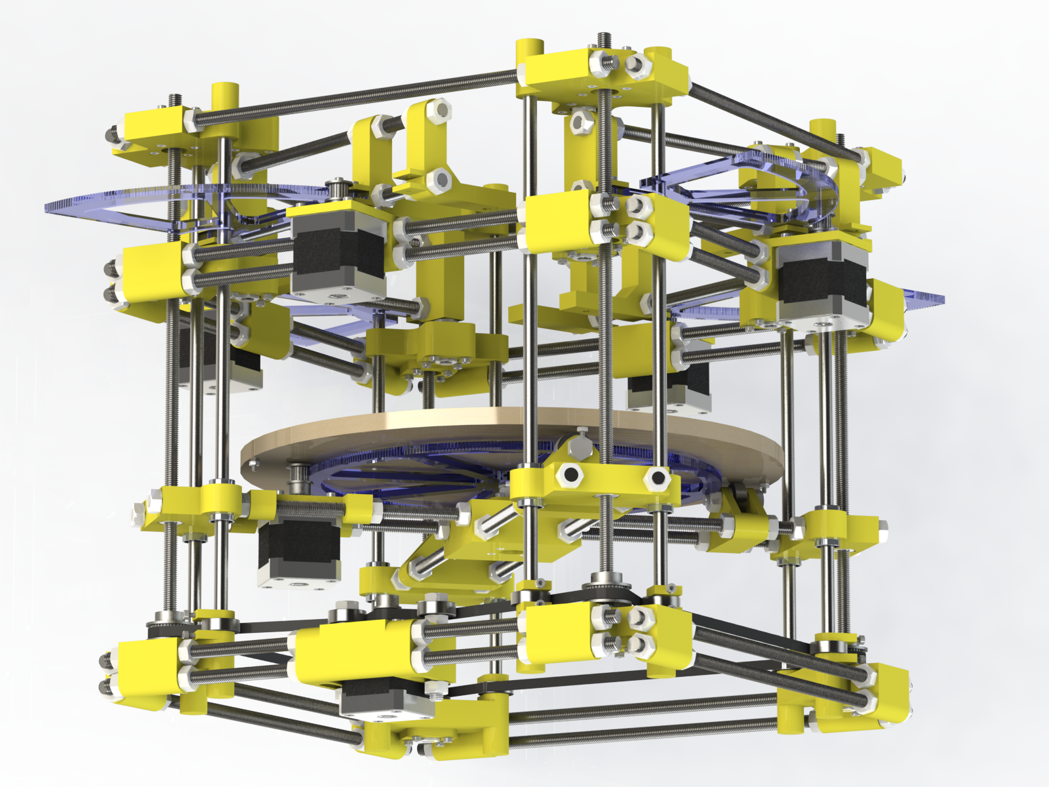
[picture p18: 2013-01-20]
Renders/theta_printer_10.png

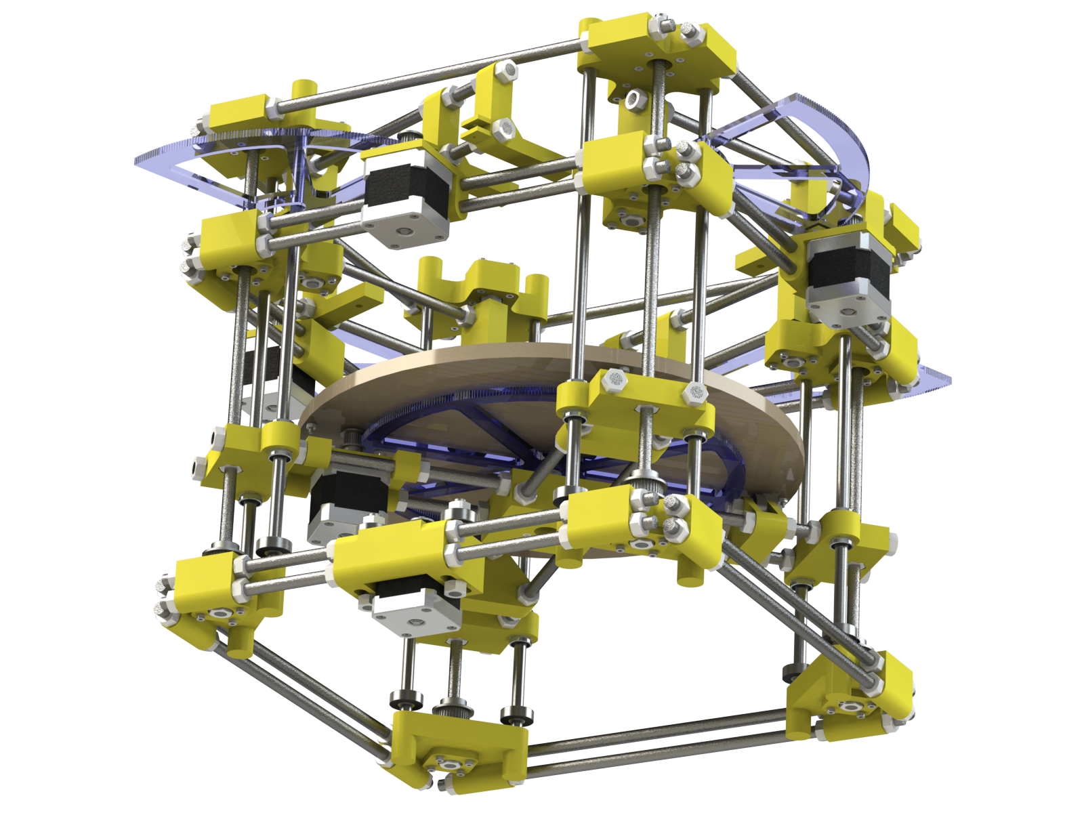
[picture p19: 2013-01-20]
Renders/theta_printer_8.png

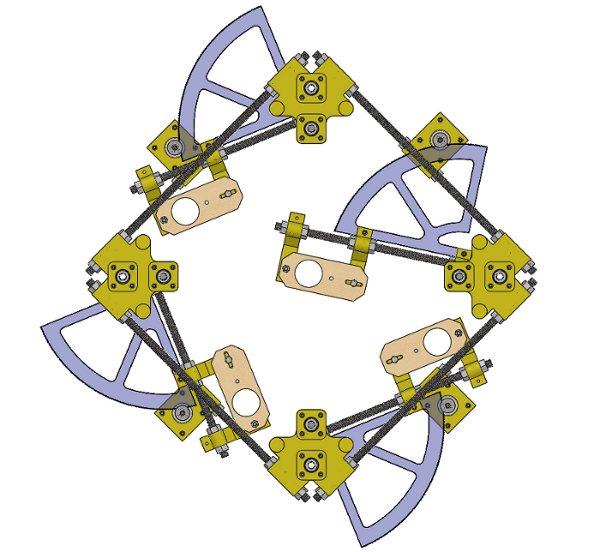
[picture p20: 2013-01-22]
Renders/Top Quad Assembly Extended.scaled.png

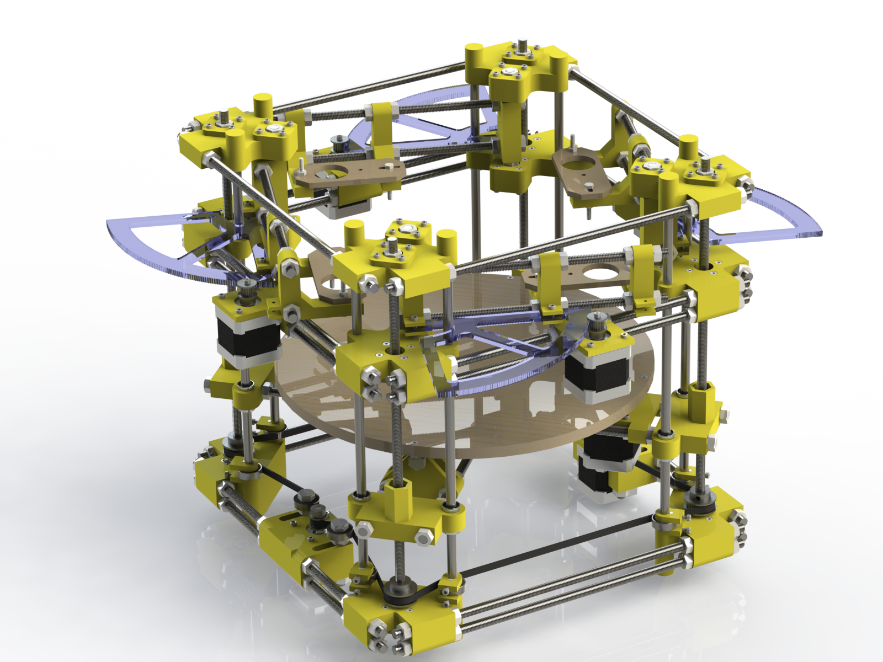
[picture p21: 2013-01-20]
Renders/theta_printer_11.png

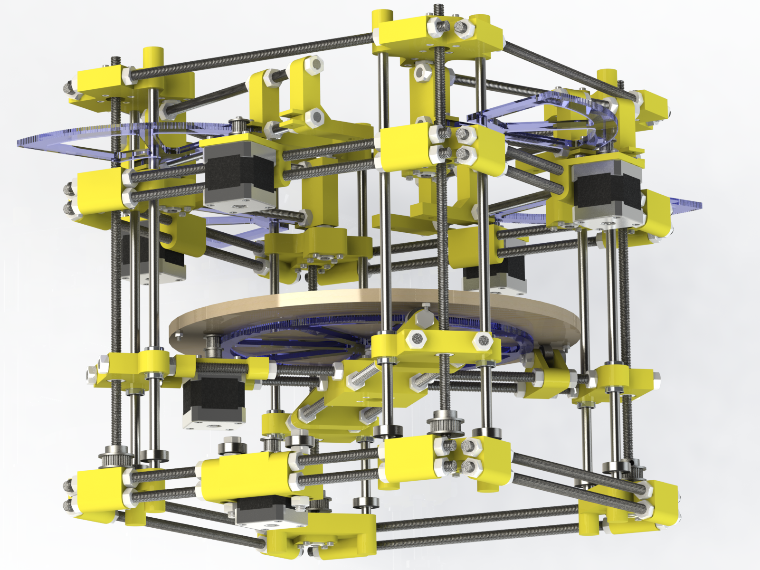
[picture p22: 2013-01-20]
Renders/theta_printer_9.png

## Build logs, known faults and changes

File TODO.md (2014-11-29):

* Square nuts
* Shallower captive nut holes on the big square
* Even gear ratio on theta (so theres an even number of steps per rotation)
* tolerances (rod holes, bearing holes, captive nuts, etc.)
* Thicken frame near Z tensioners and other thin spots
* Move tensioners farther from motors so washers don't cover motor mounting bolts
* theta gear with teeth on inside, bolted to platter around perimeter, with rollers under the gear
* way to adjust theta motor position
* Arange rollers in proper tripod
* slice top off theta drive gear
* method for adjusting phase between halves of theta gear, to eliminate play
	* Use 3 layers. Horizontal screw in middle layer to adjust phase.
* deeper teeth on theta gear
* Z smooth rods are slightly longer than 400mm. add room in level 4 corners
* platter does not fit out through sides
* M3x16 bolts are not long enough to reach through corners. recommend M3x20
* Procedure for aligning level Z with smooth rods: assemble frame with 2 sides only and level z in middle. push in smooth rods through bottom. adjust level z corner nuts until rods align with level 2 holes
* Hammer smooth rods into bottom corners first.
* You doofus. The extruders collide when one moves into the center. Even when the rest are fully retracted.
* Screwdriver notches on printed parts, to easily pry them off the print surface.
* Extend endstop mount slots to the left.
* Locks that slide onto hex nuts on the arm shafts. This will hold the arms in place when not in use and hold the nuts so you can torque things for assembly/callibration.
* The platter can unscrew itself from the shaft at inconvenient times (for example, during your senior design project presentation).
* Notches in frame to allow middle section rods to be unscrewed. Or better yet, some better means for detatching/removing the Z section. How about hinged clamp things on the corner pieces so you can detatch the middle section rods.
* Z probe
* Don't make extruders out of PLA
* Bowden extruders. Imagine 4 Krakens O_o
* Threaded rods should slide freely through printed parts
* Collision switches on extruders
* Extruder arm rods should be arranged horizontally instead of vertically.
* Bed heater needs 24V PSU and probably slip ring rated for higher power.
* Bed thermistor is probably totally wrong
* Opto sensor for homeing platter. This is not critical but could be useful for restarting paused prints.
* Connect platter gear to motor with belt.
* Need some way to clean nozzles when switching extruders
* **Ditch the whole bipolar thing and rebase everything on the R-360**
	* option for independent Z axis or locked Z axis
* Motor dampers

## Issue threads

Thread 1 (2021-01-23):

Straight R axis

n0p0n3, 2021-01-23:
I was wondering if the R axis has to be curved, or if it could be straight. Im think of a system of either linear actuators or a showerhead like matrix as a print head for a electrodisposition based system

n0p0n3, 2021-01-24:
Also, i’ve seen that you can merge the theta and z axis to have one motor with high pitch count thread do both, ie have one complete rotation of the theta axis raise the z axis by one mm or so. Do you have any thoughts on how well this would work, or problems with this method?

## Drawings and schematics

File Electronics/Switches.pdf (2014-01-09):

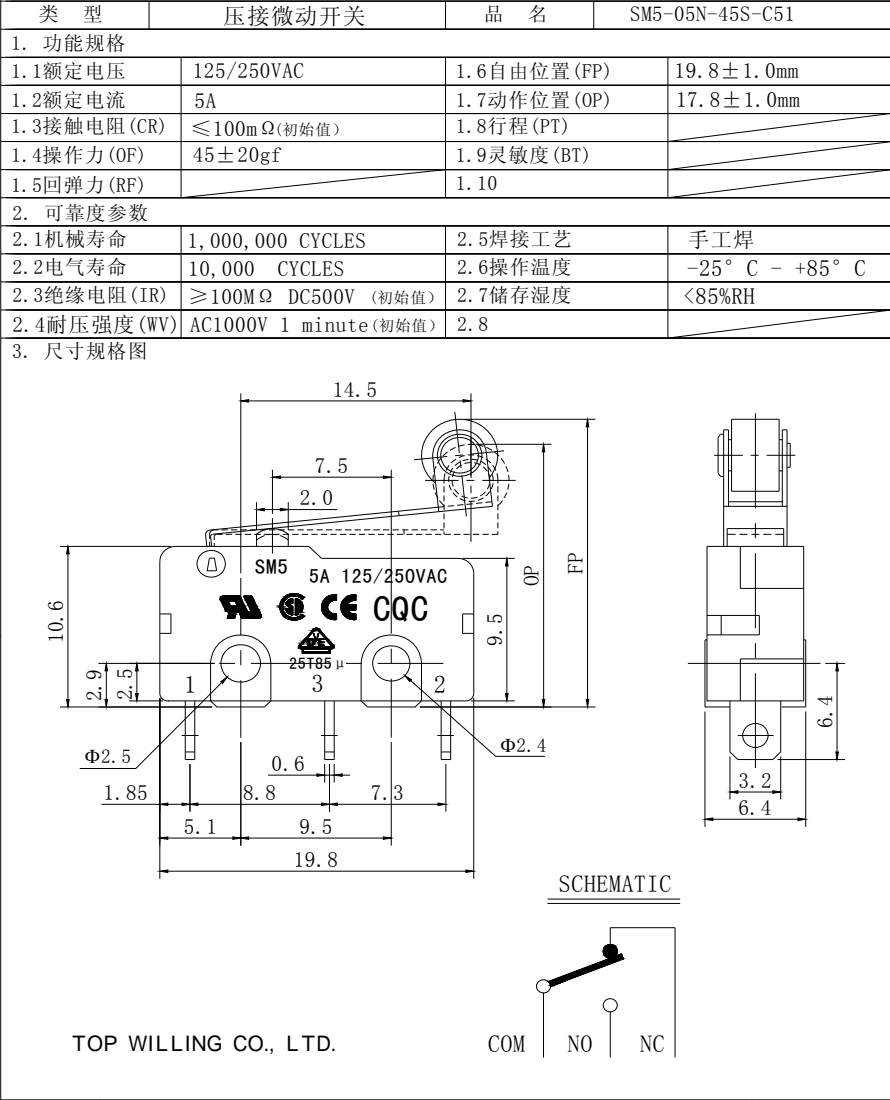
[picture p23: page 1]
COM; SCHEMATIC; 压接微动开关; (初始值）; 1.6自由位置(FP) 1.7动作位置(OP) 1.8行程(PT); 2.6操作温度; 2.5焊接工艺; 1.9灵敏度(BT); 1.1额定电压; 1. 功能规格; 1.2额定电流 1.3接触电阻(CR); 1.5回弹力(RF); 2.2电气寿命; 2.1机械寿命; 2. 可靠度参数; 1.4操作力(OF); 2.7储存湿度 2.8; 3. 尺寸规格图; 2.4耐压强度(WV); 2.3绝缘电阻(IR); 125/250VAC 5A ≤100mΩ; 1,000,000 CYCLES 10,000 CYCLES ≥100MΩ DC500V AC1000V 1 minute; 手工焊; SM5 5A 125/250VAC CQC

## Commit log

2013-01-20 First release
    [3mm Nylon Nut.SLDPRT, 3mm X 8 SET SCREW ( Mcmaster 92015A105).SLDPRT, 608 Bearing Cap.SLDPRT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]
2013-01-22 Bill of materials, documentation
    [Bill of Materials.SLDDRW, Bill of Materials.csv, Bill of Materials.ods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]
2013-01-23 Remove extruder placeholder
    [Assembly.SLDASM, Fan.SLDPRT, MBE Chassis Block.SLDPRT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]
2013-01-24 Top sketch
    [Level 1 Corner.SLDPRT, Top Side.SLDPRT, Top Sketch.SLDPRT]
2013-01-25 Top Assembly
    [Arm Axis Rod.SLDPRT, Arm Center.SLDPRT, Arm Rod.SLDPRT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]
2013-01-25 Started bottom assembly
    [Level 1 Corner.SLDPRT, Level 1 Side.SLDPRT, Level 4 Corner.SLDPRT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]
2013-01-26 Bottom side
    [Belt1-1.sldprt, Bottom Sketch.SLDPRT, Level 4 Side.SLDPRT]
2013-01-27 Z axis
    [Belt1-1.sldprt, Bottom Sketch.SLDPRT, Extruder Mount Plate.SLDPRT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]
2013-02-01 R motor assembly
    [R Motor Assembly.SLDASM, R Motor Mount.SLDPRT]
2013-02-02 Attatched R motors
    [Arm Axis Rod.SLDPRT, Arm Center.SLDPRT, Arm Rod.SLDPRT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]
2013-02-03 Fixed conflict between Z corners and frame
    [Level Z Corner Assembly.SLDASM, Level Z Corner.SLDPRT, NEMA 17.SLDASM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]
2013-02-06 Lasercut bill of materials
    [Bill of Materials.SLDDRW, Lasercut Parts.csv]
2013-02-06 Optional printed sprockets
    [Motor.Sprocket.Printed.SLDPRT, Z.Rod.Sprocket.Printed.SLDPRT]
2013-02-07 bug fixes
    [Belt1-1.sldprt, Level 4 Corner.SLDPRT, NEMA 17.SLDASM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]
2013-02-10 Sprocket fixes
    [Motor.Sprocket.Printed.SLDPRT, Motor.Sprocket.Printed.STL, Z.Rod.Sprocket.Printed.SLDPRT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]
2013-02-11 Gear stuff
    [Motor.Sprocket.Printed.SLDPRT, Motor.Sprocket.Printed.STL, Z.Rod.Sprocket.Printed.SLDPRT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]
2013-02-13 Got rid of idlers
    [Arm Axis Rod.SLDPRT, Arm Center.SLDPRT, Arm Rod.SLDPRT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]
2013-02-18 Exact sheet thickness & fewer parts
    [Arm Axis Rod.SLDPRT, Arm Center.SLDPRT, Arm Rod.SLDPRT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]
2013-02-18 Z height
    [608 Bearing Cap.SLDPRT, 608RS Bearing.SLDPRT, Arm Axis Rod.SLDPRT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]
2013-02-19 Deleted stuff
    [608 Bearing Cap.SLDPRT, Arm Center.SLDPRT, Belt1-1.sldprt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]
2013-02-23 Printed part refinements
    [Head Holder.SLDPRT, Head Holder.STL, R Motor Mount.SLDPRT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]
2013-02-24 Adjusted top frame spacing
    [Arm Axis Rod.SLDPRT, Arm Center.SLDPRT, Arm Rod.SLDPRT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]
2013-02-25 Lasercutting files
    [608 Bearing Cap.DXF, Extruder Mount Plate.DXF, Level 1 Side.DXF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]
2013-03-03 stuff idk
    [Arm Center.SLDPRT, Arm Center.STL]
2013-03-17 Printable platter rollers
    [Arm Axis Rod.SLDPRT, Arm Center.SLDPRT, Arm Rod.SLDPRT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]
2013-03-26 New platter rollers
    [Platter Roller Assembly.SLDASM, Platter Roller Side.High.DXF, Platter Roller Side.Low.DXF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]
2013-04-04 Printing tolerance
    [Level 1 Corner.STL, Level 4 Corner.SLDPRT, Level 4 Corner.STL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]
2013-04-04 BOM update
    [Lasercut Parts.xls]
2013-07-05 added tolerances to head holder
    [Head Holder.SLDPRT, Head Holder.STL, Lasercut Parts.xls]
2013-07-20 Expanded extruder mount plate to fit Budaschnozzle
    [Arm Axis Rod.SLDPRT, Arm Center.SLDPRT, Arm Rod.SLDPRT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]
2013-07-22 Updated extruder BoM
2013-08-23 Organize materials lists
    [Bill of Materials.csv, Bill of Materials.ods, CAD Parts.SLDDRW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]
2013-10-05 Electronics Power Budget
2013-10-05 Aluminium Platter
    [Platter Assembly.SLDASM, Platter Bottom.SLDPRT, Platter Top.SLDPRT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]
2014-01-09 Arm Endstops
    [Endstop Mount Assembly.SLDASM, Endstop Mount.SLDPRT, Endstop Mount.STL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]
2014-01-09 Extruder Fan Mounts
    [Extruder Fan Mount.SLDPRT, Extruder Fan Mount.STL, Extruder Fan Mount.stp]
